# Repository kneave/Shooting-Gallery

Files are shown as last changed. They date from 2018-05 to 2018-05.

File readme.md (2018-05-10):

# NERF Gun Shooting Gallery
First off, this has nothing to do with Hasbro or NERF themselves, I'm just a big fan of the toys and this seemed a fun game to make.

This repository contains all the files needed to build a NERF based shooting gallery.  It was built while mostly sleep deprived so it isn't without its quirks...  It is based around an Arduino Mega controlling a bunch of servos, WS2811 RGB LEDs and IR sensors.  The game board was laser cut and the rest of the parts were 3d printed.  **Note**,
I made a bunch of rookie errors on this and though the resulting product works, use it as a base rather than assuming it'll work out of the box.

# Overview
The idea behind this game is that it would be easy for the games team to run at the Reading Beer Festival, namely that it keeps track of its score and the targets reset.  To that end I designed a target hinge that contained a servo to reset the target once hit along with a sensor to detect a hit in the first place.

## Electronics
The electronic heart of this project is an Arduino Mega with an Adafruit PWM Servo shield.  Connected to it are:-
 - [Six WS2811 RGB LEDs](https://coolcomponents.co.uk/products/digital-rgb-addressable-led-5mm-through-hole-10-pack)
 - Six 9G hobby servos
 - [Five QTR-1A IR sensors ](https://www.pololu.com/product/958)
 - Four momentary buttons, one illuminated (optional)

The pins used are as follows:
- [Analog] 8, 9, 10, 11, 12: IR sensors
- 32: WS2811 LED pin
- 37: Reset button LED (with limiting resistor)
- 41: Reset button
- 42: IR sensor emitter pin
- 43: Set button
- 45: Up button 
- 47: Down button

The servos are connected to connections 0-5 with 0 being the points gauge. 
 
## Backboard
The backboard is was lasercut at rlab.org.uk out of transparent acrylic.  When I cut the board I was inexperienced with the laser cutter software and the result is slightly smaller than the SVG.  As a result the 3D printed parts are scaled to fit what was cut, not what was designed.  You could either scale the file to match the 3D printed components or tweak them to fit the original design.  Or just do your own thing which is what I'd recommend!

## 3D Printed/Lasercut Components

The majority of components in this game are 3D printed, as mentioned above they are scaled for the size my board ended up being rather than designed so triple check that everything will match and learn from my mistake!  

- 45deg_LED_holders.stl, rendered file for the 45 degree LED holders
- LED_holders.scad, source file for the above
- button_bracket.stl, rendered file for the button holder bracket
- button_bracket.scad, source for the above
- counter arm.stl, an arm for the point gauge but also used as the arm to reset the targets
- parametric arm.scad, source for the above
- points gauge.stl, a simple 0..100 analogue gauge
- points gauge.scad, source for the above
- Target.dxf, DXF file of the backboard
- Target.svg, SVG of the above
- target_arm_10p.stl, an arm that holds the 10 point target
- target_arm_25p.stl, an arm that holds the 25 point target
- target_arm_5p.stl, an arm that holds the 5 point target
- target_hinge.stl, a rendered file for the hinge that holds the target arm, servo and sensor
- target_hinge.scad, source for the above but also, confusingly, the target arms...
- target_scores.stl, rendered file that contains an embossed marker to go on each target
- target_scores.scad, source for the above

## QTR-1A IR Sensors
I had a bunch of these sensors and I though that they'd be a great fit for this game, the target would never physically hit the sensor so should improve reliability.  Fantastic idea in theory, in practice it worked at home but not when I took it to the beer festival.  The fest is held in a large marquee outdoors and the fiery sun god was angry that weekend.  The IR from the sun swamped the sensors and rendered them useless until I cobbled together an enclosure for it using a cardboard box, gaffer tape and a few black bin bags.
In the code there are two sets of sensitivity levels for the sensors, day and night, use them accordingly.  If you're only going to use this indoors you should be fine.
## Servos
The servos I used and the servos you use may have very different min and max values to mine so you'll want to double check these values in a simple servo test sketch first.  Adafruit include one that is ideal with the servos shield library.

## WS2811 LEDs
The LEDs I used behaved oddly to start with, the CRGB colour values didn't map correctly.  Turned out that the FastLED library has a colour order variable and I needed to change it from the default to RGB for mine.  If your LEDs misbehave, this could be why.

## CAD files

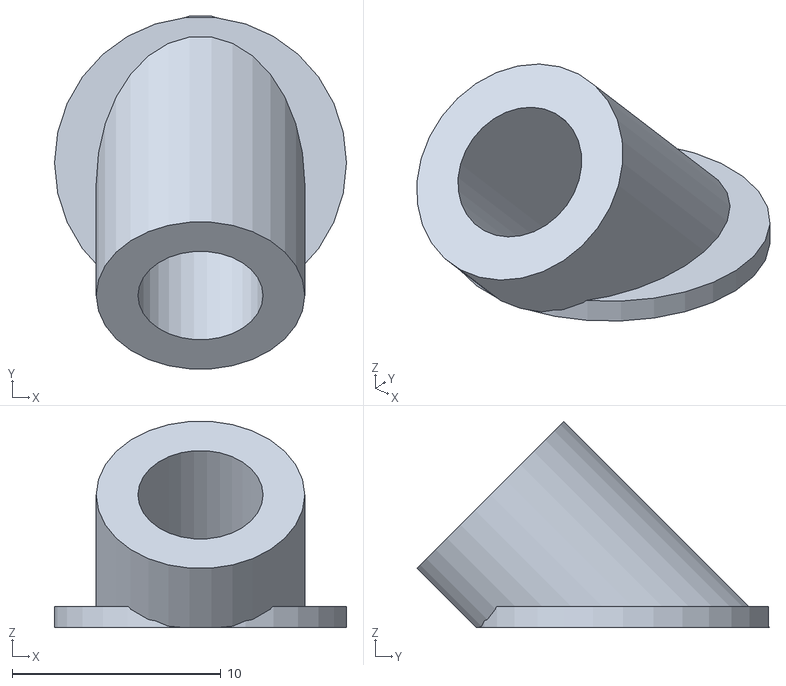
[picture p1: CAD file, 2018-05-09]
45deg_LED_holders.stl
14.0 x 16.9 x 9.88

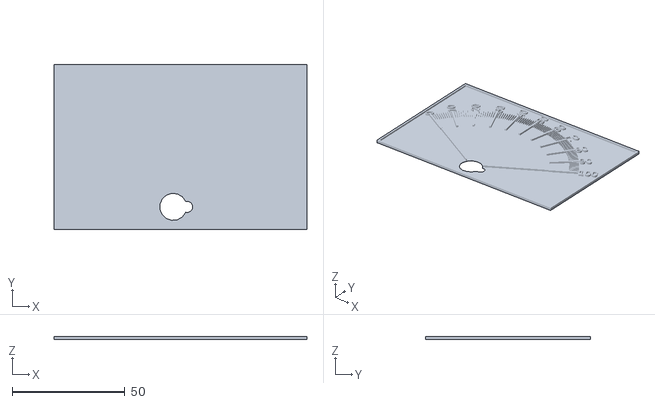
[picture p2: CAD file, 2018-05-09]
points gauge.stl
112.0 x 73.0 x 1.50

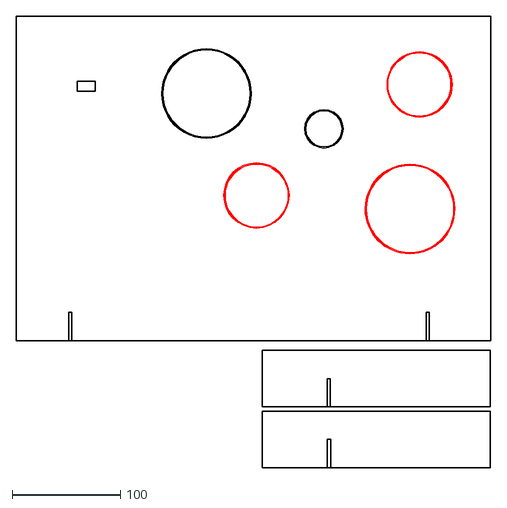
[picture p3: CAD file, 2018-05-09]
Target.dxf
437.8 x 416.3

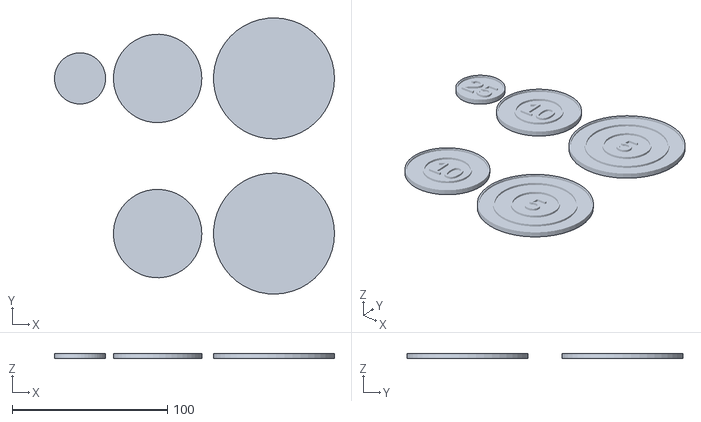
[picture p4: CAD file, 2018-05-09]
target_scores.stl
180.5 x 178.0 x 3.50

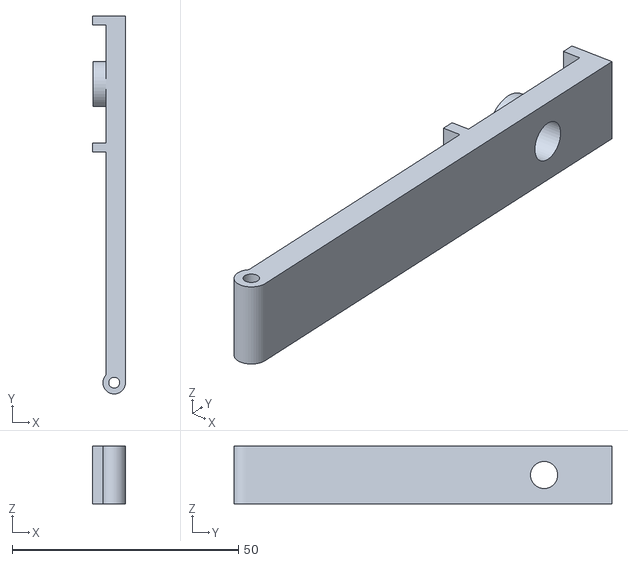
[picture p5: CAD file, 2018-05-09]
target_arm_5p.stl
7.30 x 83.5 x 12.8

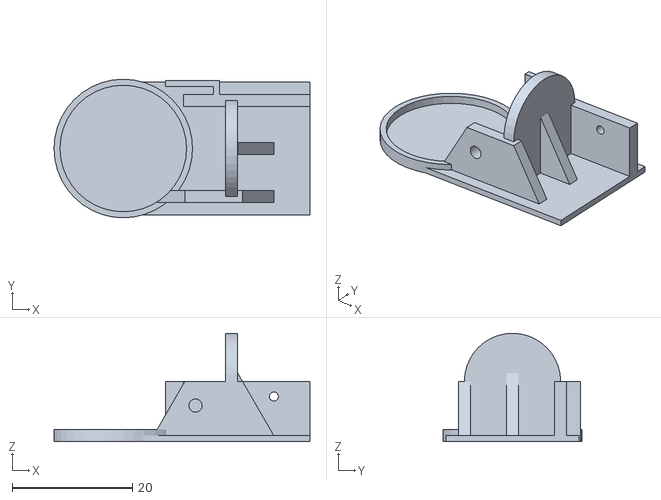
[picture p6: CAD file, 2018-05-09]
target_hinge.stl
42.5 x 23.0 x 18.0

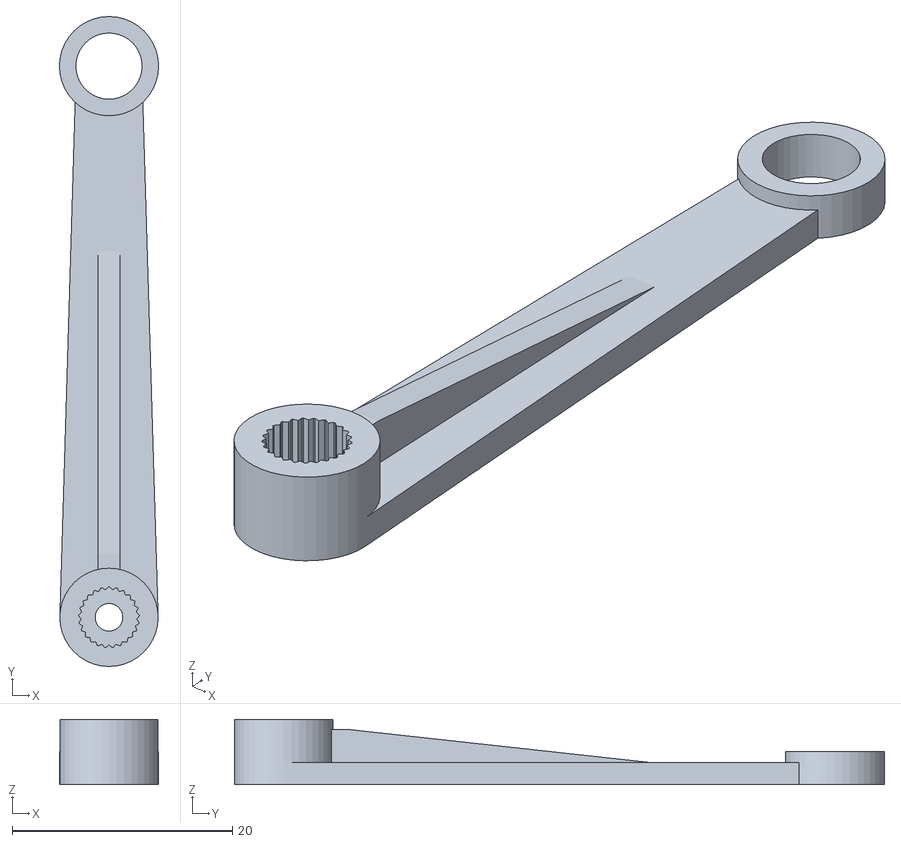
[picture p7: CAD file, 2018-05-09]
counter arm.stl
9.00 x 59.0 x 5.90

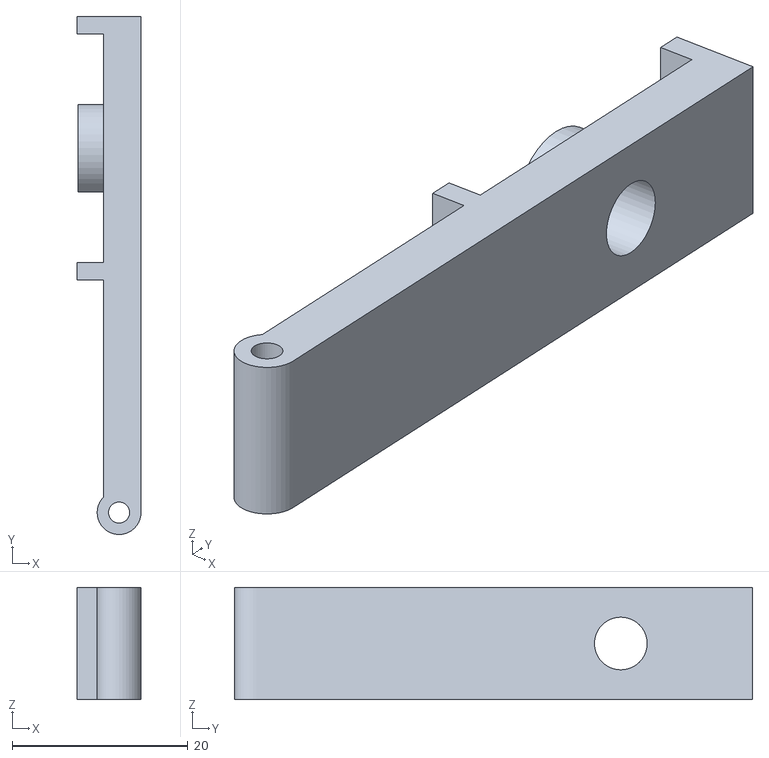
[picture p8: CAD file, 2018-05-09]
target_arm_25p.stl
7.30 x 59.0 x 12.8

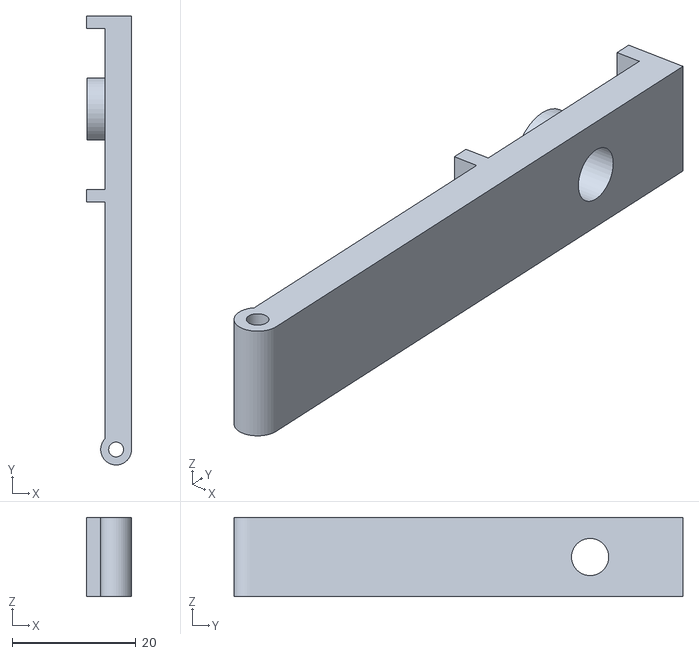
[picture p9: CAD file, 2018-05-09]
target_arm_10p.stl
7.30 x 72.5 x 12.8

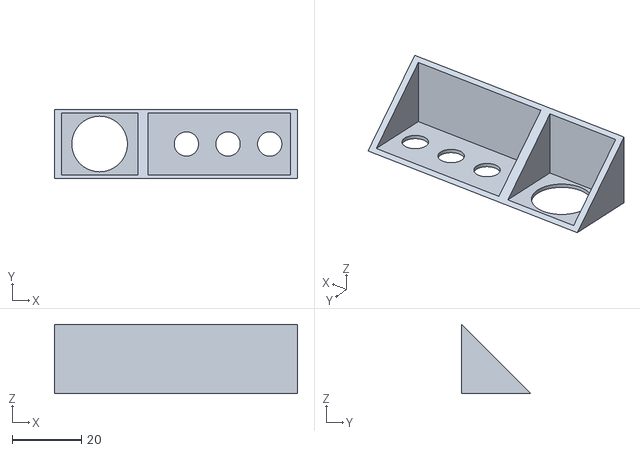
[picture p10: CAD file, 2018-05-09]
button_bracket.stl
70.0 x 20.0 x 20.0

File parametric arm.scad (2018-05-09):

/**
 *  Parametric servo arm generator for OpenScad
 *  Générateur de palonnier de servo pour OpenScad
 *
 *  Copyright (c) 2012 Charles Rincheval.  All rights reserved.
 *
 *  This library is free software; you can redistribute it and/or
 *  modify it under the terms of the GNU Lesser General Public
 *  License as published by the Free Software Foundation; either
 *  version 2.1 of the License, or (at your option) any later version.
 *
 *  This library is distributed in the hope that it will be useful,
 *  but WITHOUT ANY WARRANTY; without even the implied warranty of
 *  MERCHANTABILITY or FITNESS FOR A PARTICULAR PURPOSE.  See the GNU
 *  Lesser General Public License for more details.
 *
 *  You should have received a copy of the GNU Lesser General Public
 *  License along with this library; if not, write to the Free Software
 *  Foundation, Inc., 51 Franklin St, Fifth Floor, Boston, MA  02110-1301  USA
 *
 *  Last update :
 *  https://github.com/hugokernel/OpenSCAD_ServoArms
 *
 *  http://www.digitalspirit.org/
 */

$fn = 40;

/**
 *  Clear between arm head and servo head
 *  With PLA material, use clear : 0.3, for ABS, use 0.2
 */
SERVO_HEAD_CLEAR = 0.3;

/**
 *  Head / Tooth parameters
 *  Futaba 3F Standard Spline
 *  http://www.servocity.com/html/futaba_servo_splines.html
 *
 *  First array (head related) :
 *  0. Head external diameter
 *  1. Head heigth
 *  2. Head thickness
 *  3. Head screw diameter
 *
 *  Second array (tooth related) :
 *  0. Tooth count
 *  1. Tooth height
 *  2. Tooth length
 *  3. Tooth width
 */
FUTABA_3F_SPLINE = [
    [4.92, 4, 2, 2.5],
    [25, 0.3, 0.7, 0.1]
];

module servo_futaba_3f(length, count) {
    servo_arm(FUTABA_3F_SPLINE, [length, count]);
}

/**
 *  If you want to support a new servo, juste add a new spline definition array
 *  and a module named like servo_XXX_YYY where XXX is servo brand and YYY is the
 *  connection type (3f) or the servo type (s3003)
 */

module servo_standard(length, count) {
    servo_futaba_3f(length, count);
}

/**
 *  Tooth
 *
 *    |<-w->|
 *    |_____|___
 *    /     \  ^h
 *  _/       \_v
 *   |<--l-->|
 *
 *  - tooth length (l)
 *  - tooth width (w)
 *  - tooth height (h)
 *  - height
 *
 */
module servo_head_tooth(length, width, height, head_height) {
    linear_extrude(height = head_height) {
        polygon([[-length / 2, 0], [-width / 2, height], [width / 2, height], [length / 2,0]]);
    }
}

/**
 *  Servo head
 */
module servo_head(params, clear = SERVO_HEAD_CLEAR) {

    head = params[0];
    tooth = params[1];

    head_diameter = head[0];
    head_heigth = head[1];

    tooth_count = tooth[0];
    tooth_height = tooth[1];
    tooth_length = tooth[2];
    tooth_width = tooth[3];

    % cylinder(r = head_diameter / 2, h = head_heigth + 1);

    cylinder(r = head_diameter / 2 - tooth_height + 0.03 + clear, h = head_heigth);

    for (i = [0 : tooth_count]) {
        rotate([0, 0, i * (360 / tooth_count)]) {
            translate([0, head_diameter / 2 - tooth_height + clear, 0]) {
                servo_head_tooth(tooth_length, tooth_width, tooth_height, head_heigth);
            }
        }
    }
}

/**
 *  Servo hold
 *  - Head / Tooth parameters
 *  - Arms params (length and count)
 */
module servo_arm(params, arms) {

    head = params[0];
    tooth = params[1];

    head_diameter = head[0];
    head_heigth = head[1];
    head_thickness = head[2];
    head_screw_diameter = head[3];

    tooth_length = tooth[2];
    tooth_width = tooth[3];

    arm_length = arms[0];
    arm_count = arms[1];

    /**
     *  Servo arm
     *  - length is from center to last hole
     */
    module arm(tooth_length, tooth_width, head_height, head_heigth, hole_count = 1) {

        arm_screw_diameter = 2;

        difference() {
            union() {
                cylinder(r = tooth_width / 2, h = head_heigth);

                linear_extrude(height = head_heigth) {
                    polygon([
                        [-tooth_width / 2, 0], [-tooth_width / 3, tooth_length],
                        [tooth_width / 3, tooth_length], [tooth_width / 2, 0]
                    ]);
                }

                translate([0, tooth_length, 0]) {
                    cylinder(r = tooth_width / 3, h = head_heigth);
                }

                if (tooth_length >= 12) {
                    translate([-head_heigth / 2 + 2, 3.8, -4]) {
                        rotate([90, 0, 0]) {
                            rotate([0, -90, 0]) {
                                linear_extrude(height = head_heigth) {
                                    polygon([
                                        [-tooth_length / 1.7, 4], [0, 4], [0, - head_height + 5],
                                        [-2, - head_height + 5]
                                    ]);
                                }
                            }
                        }
                    }
                }
            }

            // Hole
            for (i = [0 : hole_count - 1]) {
                //translate([0, length - (length / hole_count * i), -1]) {
                translate([0, tooth_length - (4 * i), -1]) {
                    cylinder(r = arm_screw_diameter / 2, h = 10);
                }
            }

            cylinder(r = head_screw_diameter / 2, h = 10);
        }
    }

    difference() {
        translate([0, 0, 0.1]) {
            cylinder(r = head_diameter / 2 + head_thickness, h = head_heigth + 1);
        }

        cylinder(r = head_screw_diameter / 2, h = 10);

        servo_head(params);
    }

    arm_thickness = head_thickness;

    // Arm
    translate([0, 0, head_heigth]) {
        for (i = [0 : arm_count - 1]) {
            rotate([0, 0, i * (360 / arm_count)]) {
                arm(arm_length, head_diameter + arm_thickness * 2, head_heigth, 2);
            }
        }
    }
}

module demo() {
    rotate([0, 180, 0])
        servo_standard(20, 4);
}

difference()
{
union()
{
    rotate([0, 180, 0])
        servo_standard(50, 1);
    translate([0,50,-6]) cylinder(h=3, r=4.5);
}
    translate([0,50,-6.1]) cylinder(h=4, r=3);
}

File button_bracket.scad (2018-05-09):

$fn = 60;

difference()
{
    cube([70,22,22]);
    translate([2, 1, 1]) cube([22,22,22]);
    translate([27, 1, 1]) cube([41,22,22]);
    
    translate([-1,21,-1]) rotate([45,0,0]) cube([72,28,32]);
   
    //  Start/Reset button
    translate([13,10,-0.1]) cylinder(h=22, r=8);
    
    //  set
    translate([38,10,-0.1]) cylinder(h=22, r=3.5);
    //  up
    translate([50,10,-0.1]) cylinder(h=22, r=3.5);
    //  down
    translate([62,10,-0.1]) cylinder(h=22, r=3.5);
}

 

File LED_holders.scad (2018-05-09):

$fn=30;

difference()
{
    union()
    {
        led_holder();
    }
}
module led_holder()
{
    difference()
    {
        union()
        {            
            cylinder(h=1, r=7);
            rotate([45,0,0]) translate([0,0,-5]) cylinder(h=14, r=5);
        }
        rotate([45,0,0]) translate([0,0,-3]) cylinder(h=19.5, r=3);
        translate([-10,-10,-10]) cube([20,20,10]);
    }
}

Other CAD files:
points gauge.scad
target_hinge.scad
target_scores.scad

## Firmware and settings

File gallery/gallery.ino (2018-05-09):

//  NERF Shooting Gallery, Keegan Neave 2018

#include <QTRSensors.h>
#include <FastLED.h>
#include <Adafruit_PWMServoDriver.h>

//  Game states
enum GAME_STATE {
  Playing,
  MaxScore,
  Attract,
  Setting,
  Resetting
};

enum SETTING_LIMITS {
  Green,
  Yellow,
  Blue,
  Red
};

GAME_STATE game_state = Setting;
SETTING_LIMITS setting_limits = Green;
int score = 0;
int scores[5] = {5, 10, 25, 10, 5};

//  Timing Variables
long counter_led_millis = 0;
bool counter_led_on;

//  Buttons
#define RESET_BUTTON  41
#define SET_BUTTON    43
#define UP_BUTTON     45
#define DOWN_BUTTON   47
#define RESET_LED     37
bool reset_led_on;
long reset_button_pressed = 0;
long set_button_pressed = 0;
long up_button_pressed = 0;
long down_button_pressed = 0;

int button_pressed_debounce = 250;

// Servo variables

Adafruit_PWMServoDriver pwm = Adafruit_PWMServoDriver();
//  These are backwards because of the way the motor is mounted
#define COUNTER_MIN   448
#define COUNTER_MAX   180

#define TARGET_DOWN   200 
#define TARGET_UP     495 

//  Sensor variables
#define LeftFiveSen      0
#define LeftTenSen       1
#define TwentyFiveSen    2
#define RightTenSen      3
#define RightFiveSen     4

bool prev_values[5];
int day_sensor_levels[5] = {60, 30, 50, 70, 5};
int night_sensor_levels[5] = {100, 100, 100, 180, 100};
int sensor_levels[5] = {};
bool daytime = true;


#define NUM_SENSORS             5  // number of sensors used
#define NUM_SAMPLES_PER_SENSOR  4  // average 4 analog samples per sensor reading
#define EMITTER_PIN             42  // emitter is controlled by digital pin 2

// sensors 0 through 5 are connected to analog inputs 0 through 5, respectively
QTRSensorsAnalog qtra((unsigned char[]) {8, 9, 10, 11, 12}, 
  NUM_SENSORS, NUM_SAMPLES_PER_SENSOR, EMITTER_PIN);
unsigned int sensorValues[NUM_SENSORS];

//  LED variables
#define LED_PIN     32
#define NUM_LEDS    6
#define BRIGHTNESS  95
#define LED_TYPE    WS2812
#define COLOR_ORDER RGB
CRGB leds[NUM_LEDS];

#define CounterLED       0
#define LeftFiveLED      1
#define LeftTenLED       2
#define TwentyFiveLED    3
#define RightTenLED      4
#define RightFiveLED     5

long counter_led_prev = 0;

CRGBPalette16 currentPalette;
TBlendType    currentBlending;
bool attract_leds_set = false;

#define UPDATES_PER_SECOND 50

extern CRGBPalette16 myRedWhiteBluePalette;
extern const TProgmemPalette16 myRedWhiteBluePalette_p PROGMEM;

void setup() {
  //  Serial setup
  Serial.begin(9600); // set the data rate in bits per second for serial data transmission
  Serial.println("Gallery Comms Open...");
  Serial.println("Configuring buttons...");

  //  Button setup
  pinMode(RESET_BUTTON, INPUT_PULLUP);
  pinMode(SET_BUTTON, INPUT_PULLUP);
  pinMode(UP_BUTTON, INPUT_PULLUP);
  pinMode(DOWN_BUTTON, INPUT_PULLUP);
  pinMode(RESET_LED, OUTPUT);
  reset_led_on = false;
  
  //  LED setup
  Serial.println("Setting up LEDs...");
  delay(3000); // power-up safety delay
  FastLED.addLeds<LED_TYPE, LED_PIN, COLOR_ORDER>(leds, NUM_LEDS).setCorrection( TypicalLEDStrip );
  FastLED.setBrightness(  BRIGHTNESS );
  counter_led_on = true;
    
  //  Servo setup
  Serial.println("Setting up servos...");
  pwm.begin();
  pwm.setPWMFreq(60);

  ResetAllTargets();
   
  Serial.println("Gallery To Attract Mode...");
  game_state = Attract;

  SetAllLEDs(CRGB::Purple);

  for(int i = 0; i < 5; i++)
  {
    prev_values[i] = false;
  }

  daytime = true;
  SwitchSensorLevels(day_sensor_levels);
  
  Serial.println("Gallery Online.");
}

void loop() 
{    

  DebugSensors();

  if(digitalRead(SET_BUTTON) == 0 & SetButtonBounce())
  {
    set_button_pressed = millis();
    ResetAllTargets();
  }

  switch(game_state)
  {
    case Playing:
      CheckTargets(true);
      UpdateCounter();
      
      if(digitalRead(RESET_BUTTON) == 0 & ResetButtonBounce())
      {
        reset_button_pressed = millis();
        game_state = Attract;
      }
      break;

    case MaxScore:
    if(digitalRead(RESET_BUTTON) == 0 & ResetButtonBounce())
      {
        reset_button_pressed = millis();
        game_state = Attract;
      }
      
      if(millis() - counter_led_prev > 250)
      {
        counter_led_prev = millis();
        if(counter_led_on)
        {
          counter_led_on = false;
          leds[CounterLED] = CRGB::Black;
        }
        else
        {
          counter_led_on = true;
          leds[CounterLED] = CRGB::Red;
        }
        FastLED.show();
      }
      break;
    case Attract:
      currentPalette = RainbowStripeColors_p;
      currentBlending = LINEARBLEND;
      
      static uint8_t startIndex = 0;
      startIndex = startIndex + 1; /* motion speed */
      
      FillLEDsFromPaletteColors( startIndex);
      FastLED.show();
      FastLED.delay(2000 / UPDATES_PER_SECOND);
    
//      if(digitalRead(SET_BUTTON) == 0 & SetButtonBounce())
//      {
//        game_state = Setting;
//        setting_limits = Green;
//        set_button_pressed = millis();
//      }

      CheckTargets(false);
      
      if(digitalRead(RESET_BUTTON) == 0 & ResetButtonBounce())
      {
        reset_button_pressed = millis();
        game_state = Resetting;
      }

      if(digitalRead(DOWN_BUTTON) == 0 & DownButtonBounce())
      {
        down_button_pressed = millis();        
        daytime = !daytime;

        if(daytime == true)
        {
          SwitchSensorLevels(day_sensor_levels);
          FlashCounter(CRGB::Yellow);
        }
        else
        {  
          SwitchSensorLevels(night_sensor_levels); 
          FlashCounter(CRGB::Purple);
        } 
      }
     break;
     
    case Setting:
      //  Set button pressed, switch to next limit
      if(digitalRead(SET_BUTTON) == 0 & SetButtonBounce())
      {
        set_button_pressed = millis();
        if(setting_limits == Red)
        {
          game_state = Attract;   
          Serial.println("Red setting done, reset to Attract...");
          loop();
        }
        else
        {
          IncrementSettingLimit();
        }
      }
    
      if(millis() - counter_led_millis >= 500)
        {      
          counter_led_millis = millis();
            
          if(counter_led_on == true)
          {
            leds[CounterLED] = CRGB::Black;       
          }
          else
          {
            switch(setting_limits)
            {
              case Green:
                leds[CounterLED] = CRGB::Green; 
                break;  
              case Yellow:
                leds[CounterLED] = CRGB::Yellow; 
                break;  
              case Blue:
                leds[CounterLED] = CRGB::Blue; 
                break;  
              case Red:
                leds[CounterLED] = CRGB::Red; 
                break;  
            }      
          }
    
          counter_led_on = !counter_led_on;
          FastLED.show();
        }
      break;
      
    case Resetting:
      score = 0;
      UpdateCounter();
      ResetAllTargets();
      FastLED.show();
      game_state = Playing;
      Serial.println("Game entering play mode...");
      break;      
  }
  
//  NOTE:  The resistor I used makes the LED too weak to see so commented out for now
  ToggleResetLed();
}

//  Gameplay Methods

void SwitchSensorLevels(int newLimits[])
{
  String str = "New levels: {";
  for(int i = 0; i < 5; i++)
  {
    sensor_levels[i] = newLimits[i];
    str += String(sensor_levels[i]) + "\t";
  }

  str += '}';
  Serial.println(str);  
}

void CheckTargets(bool TrackScore)
{
  qtra.read(sensorValues);

  if(score < 100){
    HasScored(LeftFiveSen);
    HasScored(LeftTenSen);
    HasScored(TwentyFiveSen); 
    HasScored(RightFiveSen);
    HasScored(RightTenSen);
  } 
  else
  {
    if(TrackScore)
    {
      game_state = MaxScore;
      SetAllLEDs(CRGB::Red); 
    }
    else
    {
      score = 0;
    }
  }
  FastLED.show();
}

void ResetTarget(int target)
{
  //  Let the targets come to rest
  delay(500);
  pwm.setPWM(target + 1, 0, TARGET_UP);
  delay(500);
  pwm.setPWM(target + 1, 0, TARGET_DOWN);
  delay(500);
}

void HasScored(int currentSen)
{
  bool currentSenValue = sensorValues[currentSen] > sensor_levels[currentSen] ? true : false;
    
  if(currentSenValue != prev_values[currentSen])
  {    
    prev_values[currentSen] = currentSenValue;
    
    if(currentSenValue == true)
    {
      //  ie, just knocked down 
      //  Need array of ints with scores
      score = score + scores[currentSen] < 100 ? score + scores[currentSen] : 100;
      leds[currentSen + 1] = CRGB::Red;
      FastLED.show();
          
      Serial.print("Target hit: ");
      Serial.print(scores[currentSen]);
      Serial.print("\tSensor Value:\t");
      Serial.print(sensorValues[currentSen]);
      Serial.print("\tSensor Limit:\t");
      Serial.println(sensor_levels[currentSen]);

      ResetTarget(currentSen);  
    }
    else
    {
      //  Just reset
      leds[currentSen + 1] = CRGB::Green;
    }
  }
}

void UpdateCounter()
{
  //  Counter is 0..100 so set a fraction thereof
  //  Showing my working rather than just magic numbers
  //  #define COUNTER_MIN  450
  //  #define COUNTER_MAX  180
  //  diff = 450 - 180 = 270
  //  1 point = 2
  int point_servo_offset = round(2.7 * score);
  int point_servo_value = COUNTER_MIN - point_servo_offset;
  pwm.setPWM(0, 0, point_servo_value);

  //  If score less than five, stay green

  if(score >= 5) leds[CounterLED] = CRGB::White;
  if(score >= 35) leds[CounterLED] = CRGB::Yellow;      
  if(score >= 50) leds[CounterLED] = CRGB::Blue;    
  if(score >= 70) leds[CounterLED] = CRGB::Red;    

  FastLED.show();
}

void PrintScore()
{
    Serial.print("Score: ");
    Serial.println(score);
}

void ResetAllTargets()
{
  pwm.setPWM(0, 0, COUNTER_MIN);
  leds[CounterLED] = CRGB::Green;
  FastLED.show();
  delay(500);

  for(int i = 1; i < 6; i++)
  {
    leds[i] = CRGB::Red;
    FastLED.show();
    pwm.setPWM(i, 0, TARGET_UP);
    delay(500);
    pwm.setPWM(i, 0, TARGET_DOWN);
    
    leds[i] = CRGB::Green;
    FastLED.show();
  }
}

void FlashCounter(CRGB colour)
{
  for(int i = 0; i < 5; i++)
  {
    leds[CounterLED] = colour;
    FastLED.show();
    delay(500);
    leds[CounterLED] = CRGB::Black;
    FastLED.show();
    delay(500);
  }
}

//  Enum Methods

void IncrementSettingLimit()
{
  switch(setting_limits)
  {
    case Green:
      setting_limits = Yellow;
      break;    
    case Yellow:
      setting_limits = Blue;
      break;    
    case Blue:
      setting_limits = Red;
      break;    
    case Red:
      setting_limits = Green;
      break;    
  }
}

//  Button methods

bool SetButtonBounce()
{
  return (millis() - set_button_pressed > button_pressed_debounce);
}

bool ResetButtonBounce()
{
  return (millis() - reset_button_pressed > button_pressed_debounce);
}
bool UpButtonBounce()
{
  return (millis() - up_button_pressed > button_pressed_debounce);
}
bool DownButtonBounce()
{
  return (millis() - down_button_pressed > button_pressed_debounce);
}

void ToggleResetLed()
{
  if(reset_led_on)
  {
    digitalWrite(RESET_LED, LOW);
    reset_led_on = false;
  }
  else
  {
    digitalWrite(RESET_LED, HIGH);
    reset_led_on = true;
  }
}

void DebugButtons()
{
  Serial.print("Reset: ");
  Serial.print(digitalRead(RESET_BUTTON));
  Serial.print('\t'); // tab to format the raw data into columns in the Serial monitor
  Serial.print("Set: ");
  Serial.print(digitalRead(SET_BUTTON));
  Serial.print('\t'); // tab to format the raw data into columns in the Serial monitor
  Serial.print("Up: ");
  Serial.print(digitalRead(UP_BUTTON));
  Serial.print('\t'); // tab to format the raw data into columns in the Serial monitor
  Serial.print("Down: ");
  Serial.print(digitalRead(DOWN_BUTTON));
  Serial.print('\t'); // tab to format the raw data into columns in the Serial monitor
  Serial.println();
}

//  Sensor Methods

void DebugSensors()
{
    // read raw sensor values
  qtra.read(sensorValues);
  
  // print the sensor values as numbers from 0 to 1023, where 0 means maximum reflectance and
  // 1023 means minimum reflectance
  for (unsigned char i = 0; i < NUM_SENSORS; i++)
  {
    Serial.print(sensorValues[i]);
    Serial.print('\t'); // tab to format the raw data into columns in the Serial monitor
  }
  Serial.println();
  
  delay(250);
}

//  LED Methods

void SetAllLEDs(CRGB colour)
{
  leds[0] = colour;
  leds[1] = colour;
  leds[2] = colour;
  leds[3] = colour;
  leds[4] = colour;
  leds[5] = colour;  

  FastLED.show();
}

void FillLEDsFromPaletteColors( uint8_t colorIndex)
{
    uint8_t brightness = 255;
    
    for( int i = 0; i < NUM_LEDS; i++) {
        leds[i] = ColorFromPalette( currentPalette, colorIndex, brightness, currentBlending);
        colorIndex += 3;
    }
}

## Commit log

2018-05-09 Initial checkin
    [45deg_LED_holders.stl, 50mm servo arm.stl, 70mm servo arm.stl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]
2018-05-10 Added a bit of info about 3d printed components
    or at least where to contact me if I don't fill in the blanks...
2018-05-10 These aren't actually used in the current design
    [50mm servo arm.stl, 70mm servo arm.stl]
2018-05-10 Improved the list of 3d printed parts
